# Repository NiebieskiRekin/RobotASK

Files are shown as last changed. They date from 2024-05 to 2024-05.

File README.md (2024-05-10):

# Robot ASK - Piano tiles

A Piano Tiles (mobile game) hardware autoclicker built on the ATmega328. All electrical sketches and the PCB were designed in [KiCad](https://www.kicad.org/). Code for the microprocessor was written in C++ using Arduino and Servo libraries as well as the [PlatformIO](https://platformio.org/install/ide?install=vscode) VSCode extension.

This project also has a live visualisation Python script that communicates with the main board over serial to display data captured by the photoresistor module. This script can also be used to quickly adjust some parameters at the start of runtime.

This repository was created for a university group project for [RoboDay 2024](https://www.facebook.com/events/1518830758974874) at Poznań University of Technology.
Made by: Tomasz Pawłowski, Jakub Kamieniarz, Jakub Buler, Adam Deter  

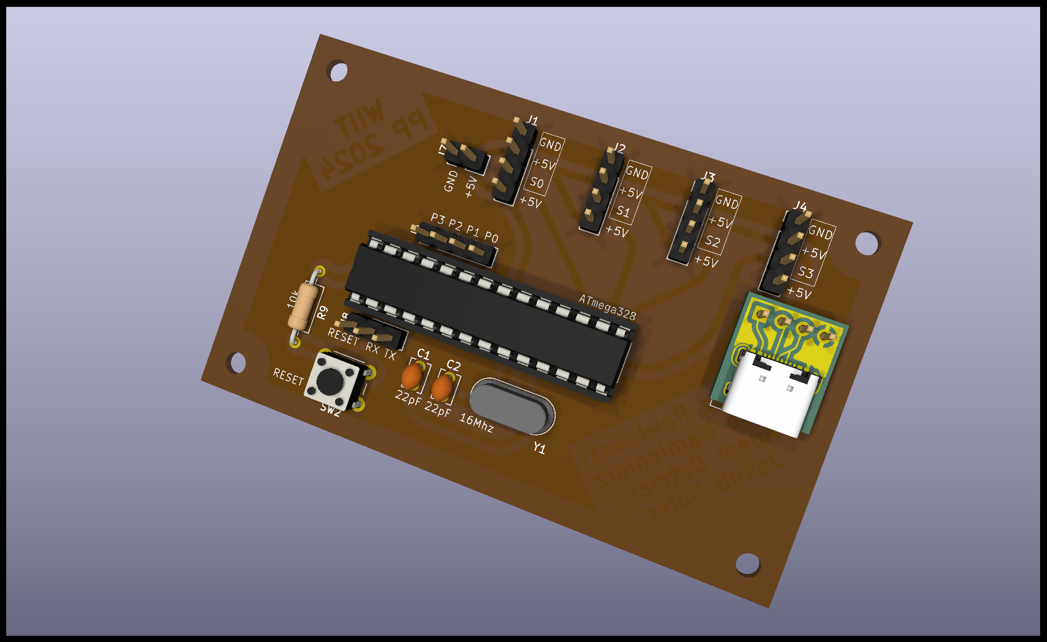
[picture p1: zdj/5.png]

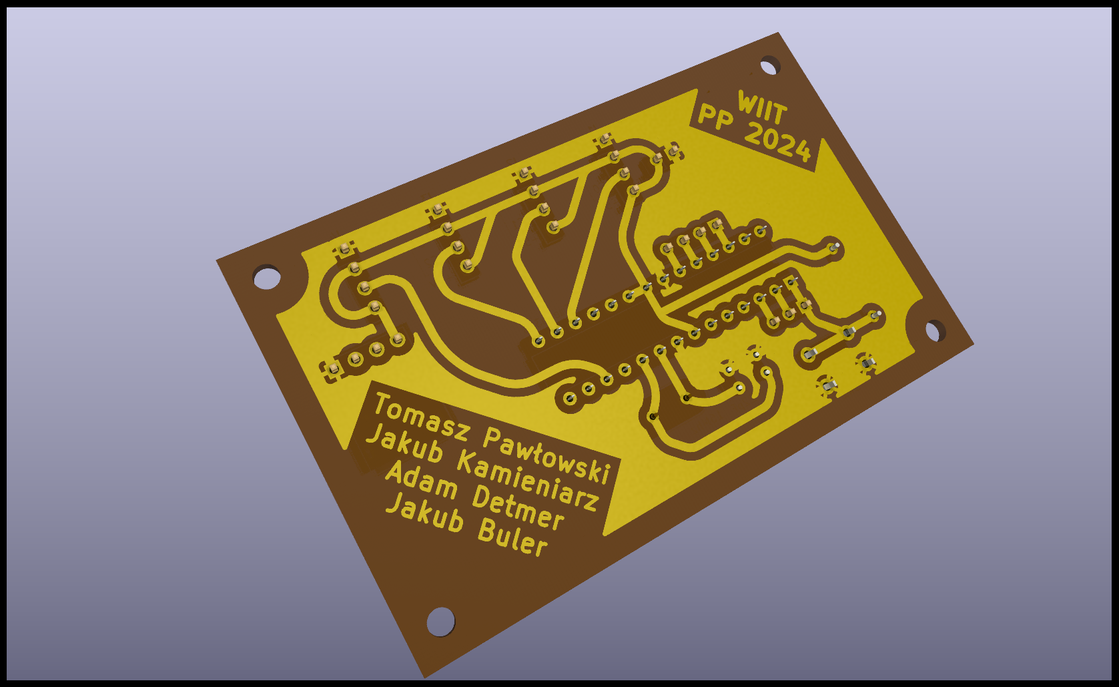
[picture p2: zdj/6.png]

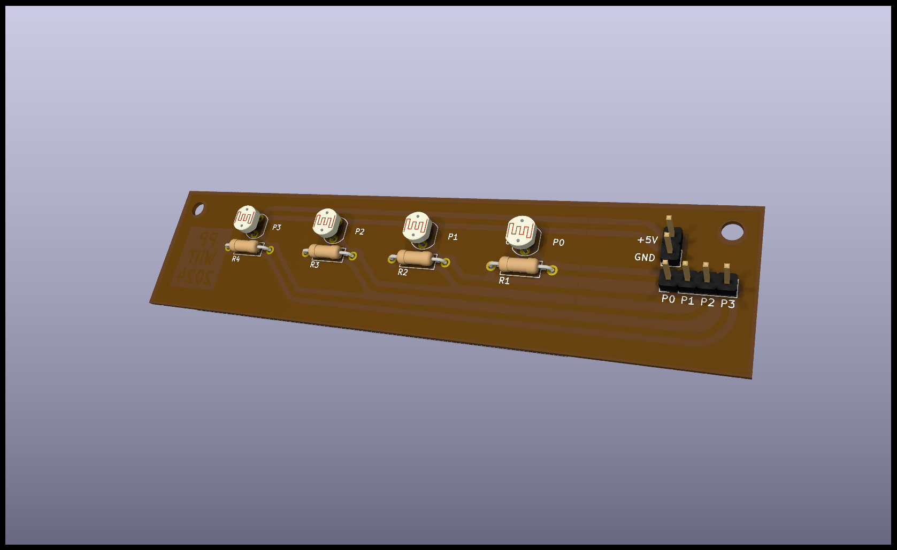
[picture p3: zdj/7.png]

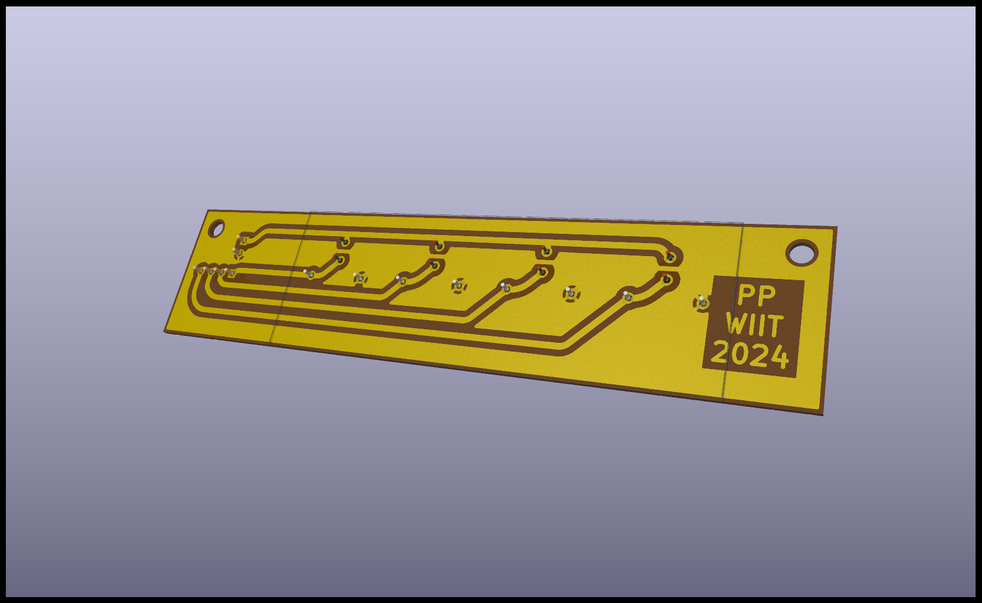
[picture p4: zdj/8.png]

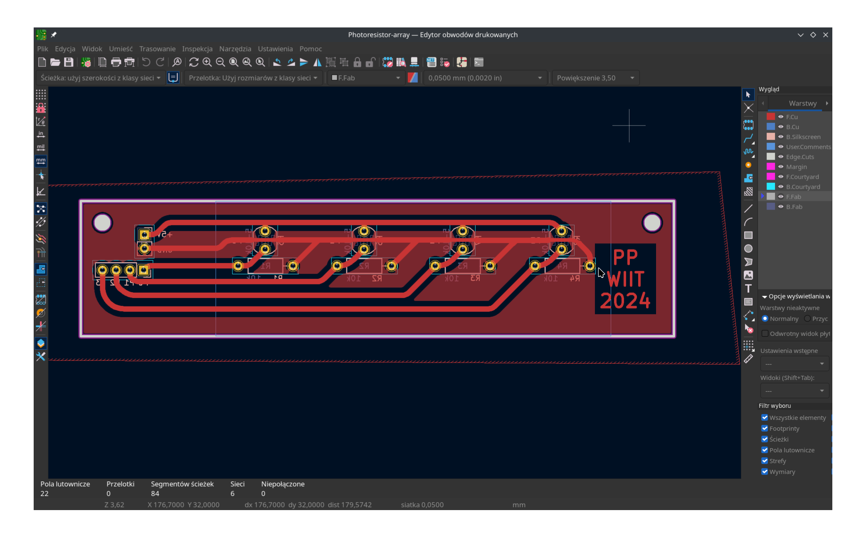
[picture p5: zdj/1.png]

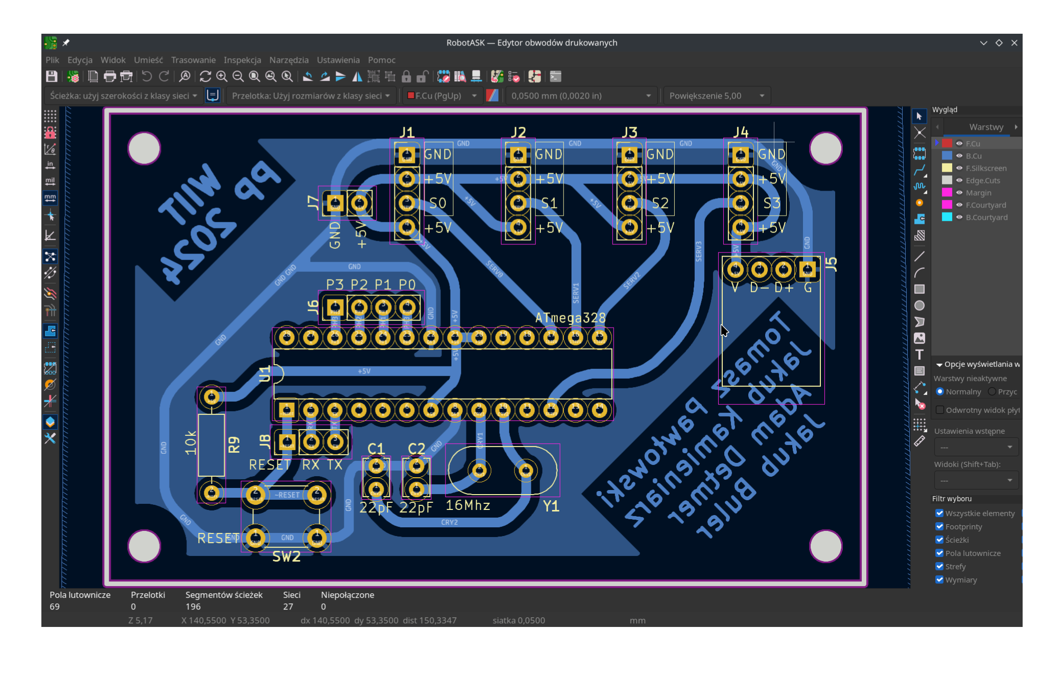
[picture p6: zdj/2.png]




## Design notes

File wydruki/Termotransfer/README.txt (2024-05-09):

Wydruk na papierze kredowym na drukarce laserowej.
Płytka z fotorezystorami jest ma piny po przeciwnej stronie względem rezystorów

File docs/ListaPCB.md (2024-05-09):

# Lista do wytrawiania PCB

## Wymiary laminatu z miedzią:
- co najmniej o 5mm dłuższe i szersze od każdej krawędzi płytki

układ 

#### Wymiary głównej płytki:
- wszerz (x) 80mm
- wzdłuż (y) 50mm
- wzwyż (z) min. 6mm (potencjalnie więcej ze względu na wpinane przewody do pinów)
- otwory na komponenty 1mm

#### Otwory na przykręcenie głównej płytki:
- średnica 3mm
- odległość środka od krawędzi 3mm
- odległość wszerz (x) pomiędzy otworami (środki) 74mm
- odległość wzdłuż (y) pomiędzy otworami (środki) 44mm

#### Wymiary płytki z fotorezystorami:
- długość płytki (x) 110 mm
- szerokość płytki (y) 17mm
- odległość pomiędzy fotorezystorami (środki) 18,325mm
- szerokość ekranu 73,3mm
- otwory na goldpiny o średnicy 1mm
- otwory na rezystory i fotorezystory 0,8mm

#### Otwory na przykręcenie płytki z fotorezystorami:
- średnica 3mm
- odległość środka od krawędzi 3mm
- odległość wszerz (x) pomiędzy środkami otworów 104mm
- odległość lewego otworu (obok pinów) do krawędzi ekranu 22mm
- odległość prawego otworu (obok napisu) do krawędzi ekranu 8,7mm
- odległość krawędzi pinu (czarnej podstawy) do krawędzi ekranu 12mm

## Wariant 1: Termotransfer
[filmik (pl)](https://www.youtube.com/watch?v=1L4GrPDR9TE)

### Lista rzeczy:

- [ ] rękawiczki i okulary ochronne
- [ ] wytrawiacz, jeden z:
  - nadsiarczan sodu
  - chlorek żelaza
  - kwas azotowy
- [ ] proszek do prania xd
- [ ] zamiennie
  - rozpuszczalnik nitro
  - benzyna ekstrakcyjna
- [ ] lejek
- [ ] plastikowa butelka (1.5l)
- [ ] plastikowa kuweta (pojemnik bez wieczka)
- [ ] laminat z jedną wartstwą miedzi (miedziana blaszka jakby)
- [ ] wodny papier ścierny
- [ ] gąbka kuchenna + mleczko do mycia (cif)
- [ ] żelazko z płaską powierzchnią grzejącą (bez pary)
- [ ] linijka + ekierka duża
- [ ] pilnik (taki do metalu)
- [ ] zamiennie
  - nożyce do laminatu
  - piłka do metalu
  - nożyk do tapet i dużo cierpliwości
- [ ] zwykłe nożyczki do papieru
- [ ] świeża szczoteczka
- [ ] ołówek
- [ ] wydruk płytki na papierze kredowym z drukarki laserowej w lustrzanym odbiciu (bez negatywu)

## Wariant 2: UV
[filmik 1 (ang)](https://www.youtube.com/watch?v=1C3k6dyVN18)
[filmik 2 (ang)](https://www.youtube.com/watch?v=xyBgbNPrWg8)

### Lista rzeczy 

to

- [ ] chemia ze zdjęcia
- [ ] laminat z warstwą miedzi
- [ ] alkohol do mycia i ściereczka
- [ ] papier ścierny
- [ ] wydruk pcb na zwykłej kartce papieru z drukarki atramentowej w odbiciu i w negatywie (high quality)
- [ ] nożyk do tapet
- [ ] dry film roll (sucha folia światłoczuła? [to](https://allegro.pl/oferta/portable-photosensitive-dry-film-pcb-in-roll-for-circuit-board-1m-blue-12340601866))

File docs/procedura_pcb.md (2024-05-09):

# Procedura pcb
1. oczyść płytkę za pomocą gąbki lub papieru ściernego
2. wydruk w negatywie i odbiciu na papierze (jaka drukarka?)
3. przytnij płytkę do wymiaru
4. naklej folię światłoczułą na plytkę
5. pozbądź się bąbelków suszarką / żelazkiem
6. na płytkę z folią posmarowaną na wierzchu olejkiem nałóż wydruk płytki tuszem do dołu
7. UV (nwm ile czasu)
8. przepłucz płytkę w roztworze NaOH lub NaCO3 ???
9. przepłucz płytkę pod bieżącą wodą
10. zakryj dziury markerem pernamentnym
11. wytrawianie płytki w FeCl3
12. oczyszczenie płytki w acetonie+szczoteczka lub NaOH znowu

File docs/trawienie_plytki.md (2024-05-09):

# Podsumowanie trawienia płytki

## Etapy:
1. Oczyszczenie warstwy miedzi z płytki wodnym papierem ściernym oraz potem alkoholem
2. Przycięcie płytki do wymiaru z zapasem za pomocą tępej strony nożyka do tapet
3. Naklejenie folii światłoczułej na płytkę bez bąbli powietrza (suszarka oddalona o parę cm), odklejenie warstwy ochronnej za pomocą taśmy malarskiej
4. Nałożenie kartki papieru z wydrukiem z drukarki laserowej na folię pokrytą olejem
5. 159 sekund naświetlania lampą UV 36W, potem odklejenie drugiej folii ochronnej
6. [nieudane] Wywołanie płytki w roztworze 1% masowych NaOH z wodą (200ml, szczoteczka, bujanie na boki), przepłukanie wodą
	- Roztwory o wyższym stężeniu (np. 5%, 2/3 łyżki stołowej na pół litra wody) sprawnie usuwają całą folię, nadają się do ostatniego etapu
	- Roztwory o niższym stężeniu (poniżej 1%) działają zbyt długo, przez co folia ulega zniszczeniu
	- Trzymanie w roztworze powyżej 2min ogólnie niszczy folię i zaciera ścieżki 
	- Przetarcie delikatne włosiem szczoteczki pomaga przyśpieszyć proces i zdjąć odpowiednie warstwy na początku, ale w momencie gdy jest już widoczna miedź to tylko psuje dalej folię
	- roztwór sody oczyszczonej (NaHCO3, słaba zasada) w żadnym stężeniu nie przyniósł efektu 
7. Wytrawianie płytki w roztworze 25% masowych FeCl3 z wodą (200ml roztworu, bujanie na boki) aż do momentu zupełnego pozbycia się śladów miedzi z pól gdzie jej nie powinno być. Przepłukanie wodą
8. Zmycie pozostałej folii w acetonie technicznym lub 5% NaOH + szczoteczka. Przepłukanie wodą
9. [nieosiągnięte] Wytrawiona płyka gotowa, nawiercenie otworów, docięcie i przeszlifowanie krawędzi płytki, wlutowanie komponentów

## Pomysły na etap nr 6
- [ ] przetestowanie innego wywoływacza (Na2CO3 lub Na2SiO3)
- [ ] pozostawienie płytki po ekspozycji UV na 10-30 min w ciemnym miejscu przed wywołaniem
- [ ] skrócenie lub przedłużenie ekspozycji UV
- [ ] przeniesienie procesów do ciemniejszego pomieszczenia
- [ ] przerobienie schematu płytki na wieksze ścieżki i odstępy między nimi
- [ ] wydruk na kalce technicznej 90g/m^2, wyższej jakości, zaczernienie nad oparami acetonu
- [ ] użycie innego oleju (np. mineralnego) zamiast rzepakowego

## Inne notatki
- aby zmyć folię acetonem to trzeba zanurzyć płytkę na kilkadziesiąt sekund i zetrzeć mechanicznie
- olej rzepakowy (kujawski itd) sprawdza się dobrze do nakładania wydruku na folię, aby zapewnić przezroczystość
- dopóki płytka nie przeszła wytrawiacza to nieudany etap wywoływania można przywrócić do kroku 3. naklejania folii światłoczułej poprzez zmycie resztek folii acetonem
- poszukaj więcej plastikowych łyżek i łyżeczek oraz uszykuj baniaki z wodą 
- prażenie sody oczyszczonej (NaHCO3) daje węglan sodu (Na2CO3), który ma silny odczyn zasadowy i może przyniesie lepszy efekt
- w tutorialach używane są lampy o dużo słabszej mocy i różnym czasie naświetlania (jedni piszą 20 sekund inni 10 minut)
	- stary skaner z zamontowanymi w środku czterema świetlówkami UV 9W przez 25s
	- lampa do tipsów 9W przez 15-20s

	> "Po naświetleniu zrywam folię przezroczystą z nalepionej na płytkę folii światłoczułej i odkładam płytkę w ciemne miejsce na 10 minut. Jest to konieczne, aby zaszły pewne procesy w polimerze"

	> "Ustawiamy czas naświetlania. Jeżeli nasza naświetlarka nie ma możliwość ustawiamy minutnik na 2 do 4 minut. Czas jaki jest potrzebny zależy od naszej naświetlarki a dokładniej żarówek jakie zastosowaliśmy. Po naświetlaniu zostawić płytkę w ciemni na około 30 min. Może to być również szczelne pudełko lub inne ciemne miejsce gdzie promienie światła ani słońca nie będą mogły dojść do płytki."

- Wydruk wyższej jakości na kalce technicznej 90g/m^2 - grubszy papier

> "Następny krok to nawiercanie. Wszystkie dziurki robię na wiertarce ze statywem wiertłami z węglika VHM. Prędkość wrzeciona to 20 tys. obrotów na minutę oraz posuw w osi Z 150mm/min" 

- Praca nad płytką od momentu oczyszczenia płytki wykonywana w piwnicy lub łazience aż do momentu wytrawienia w wytrawiaczu
- powszechnie używane wywoływacze:
	- metakrzemian disodu (Na2SiO3, ten z woreczka "wywoływacz"), [przykladowy link](https://www.tme.eu/pl/details/uni-dev-22g/materialy-do-produkcji-plytek-drukow/ag-termopasty/art-agt-087/), roztwór 10g/1l
	- soda kalcynowana (Na2CO3), **prażona** soda oczyszczona, niżej proces prażenia, Stężenie roztworu wywoływacza to 5g na 0,5 l wody, 
	- do folii nie nadaje się żaden roztwór NaOH 

> "soda kalcynowana, którą można kupić w sklepach internetowych lub wykonać samodzielnie z sody oczyszczonej: blachę wyłożyć papierem do pieczenia, wysypać sodę i wstawić do rozgrzanego do 200 stopni C piekarnika na godzinę" [link](https://zielonyogrodek.pl/dom-i-balkon/porady-domowe/15606-czy-mozesz-samodzielnie-zrobic-tabletki-do-zmywarki-tak-i-to-bardzo-latwo-oto-nasze-przepisy)

- użycie lepszego środka do sprawienia że kartka zrobi się przezroczysta na folii
	- naj. oleje mineralne
	- baby oil
	- WD40/transparent

> "Jak folia jest negatywowa, to wywoływaczem jest węglan sodu, jak pozytywowa to wodorotlenek sodu lub metakrzemian. "

## Tutoriale:
1. [https://www.leniwiec.org/2014/03/02/moja-metoda-robienia-pcb-metoda-fotochemiczna-z-soldermaska-cynowaniem-i-opisami/ ](https://www.leniwiec.org/2014/03/02/moja-metoda-robienia-pcb-metoda-fotochemiczna-z-soldermaska-cynowaniem-i-opisami/ )
2. [http://gotronik.com/2019/09/18/jak-zrobic-plytke-pcb-metoda-fotochemiczna/](http://gotronik.com/2019/09/18/jak-zrobic-plytke-pcb-metoda-fotochemiczna/)
3. [https://www.elektroda.pl/rtvforum/topic2527723.html](https://www.elektroda.pl/rtvforum/topic2527723.html)
4. [https://www.elektroda.pl/rtvforum/topic2714312.html](https://www.elektroda.pl/rtvforum/topic2714312.html)

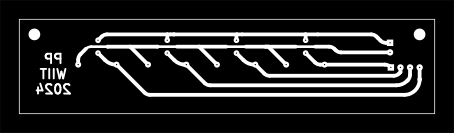
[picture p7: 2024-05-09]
wydruki/UV/new/g3.png

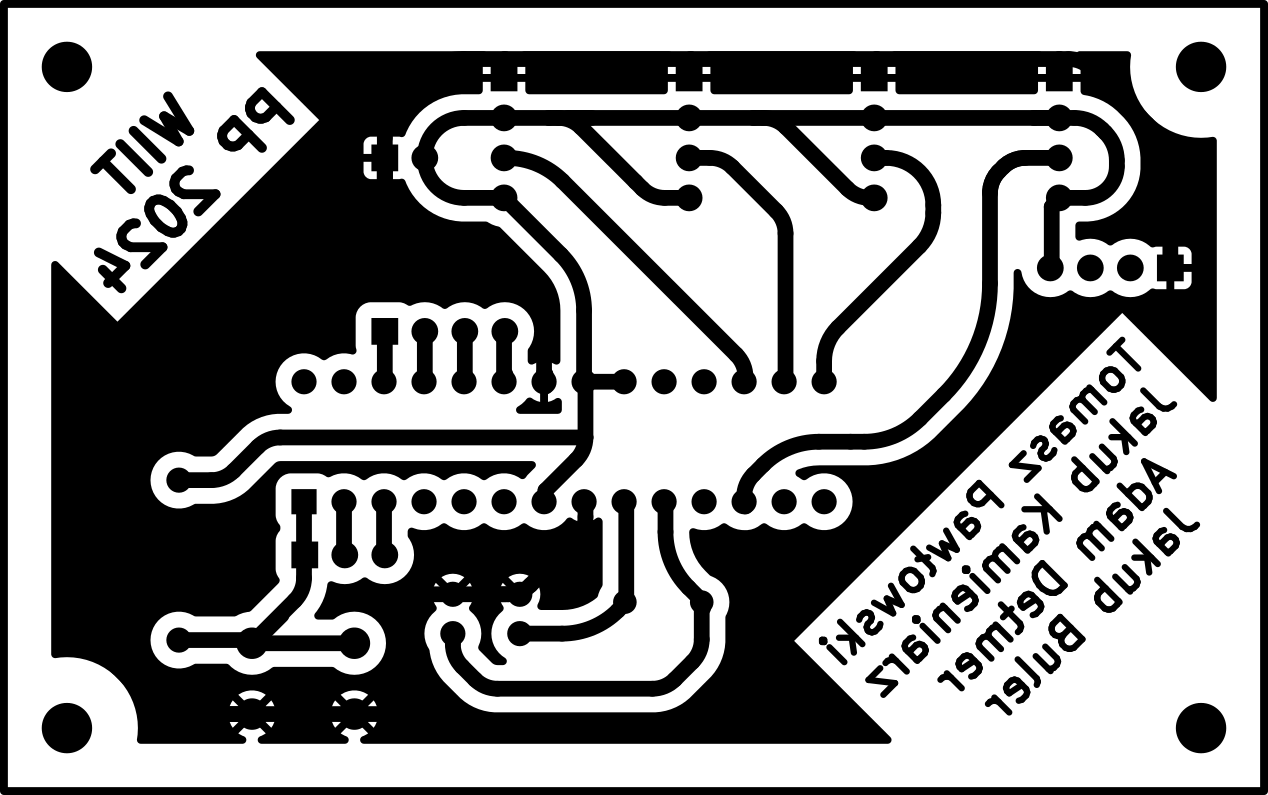
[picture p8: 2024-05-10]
wydruki/Termotransfer/v2/RobotASK-B_Cu.png

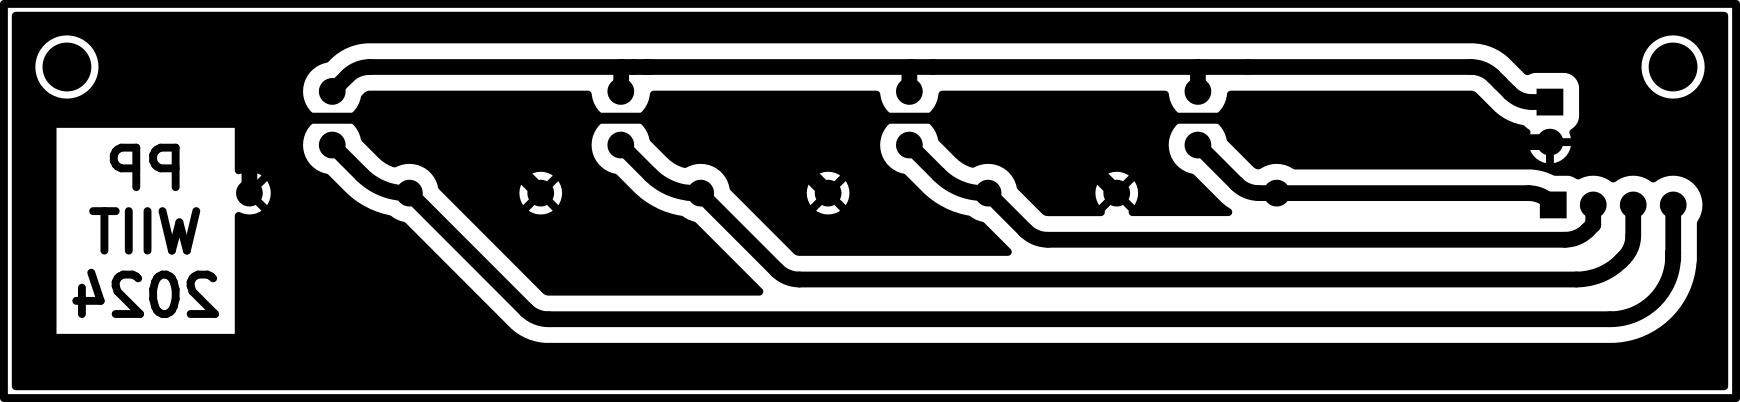
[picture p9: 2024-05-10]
wydruki/Termotransfer/v2/Photoresistor-array-F_Cu.png

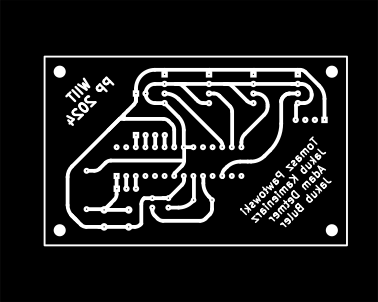
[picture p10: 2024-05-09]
wydruki/UV/new/g2.png

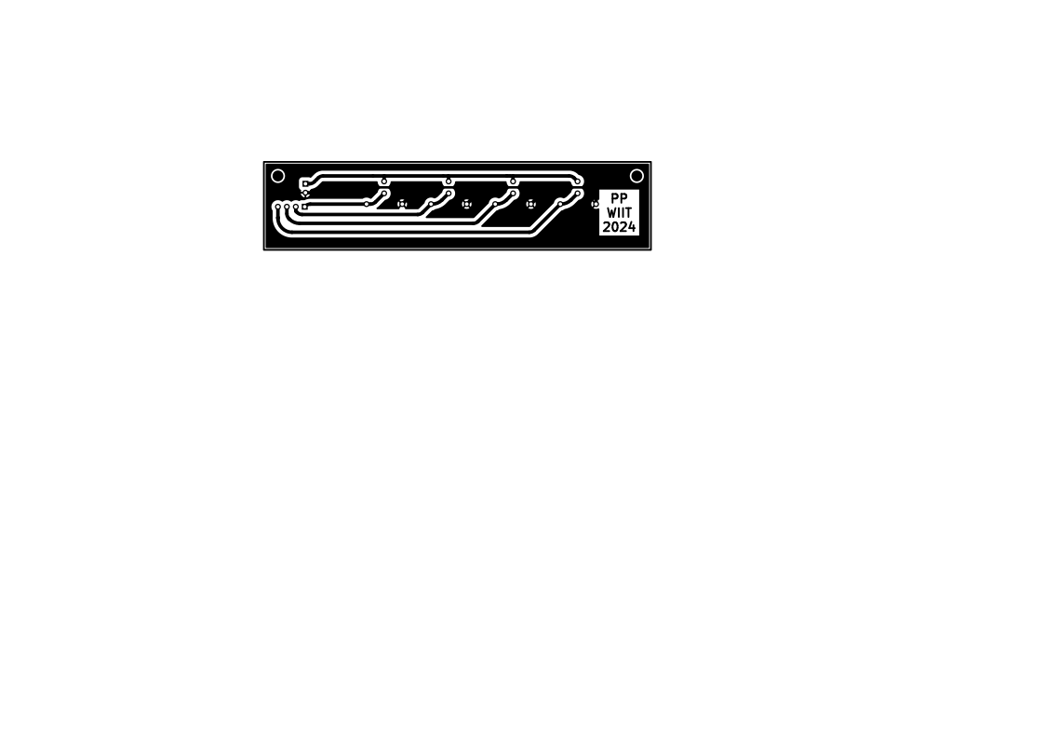
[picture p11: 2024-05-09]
wydruki/wiercenia/Photoresistor-array-skala-1-znaczniki.png

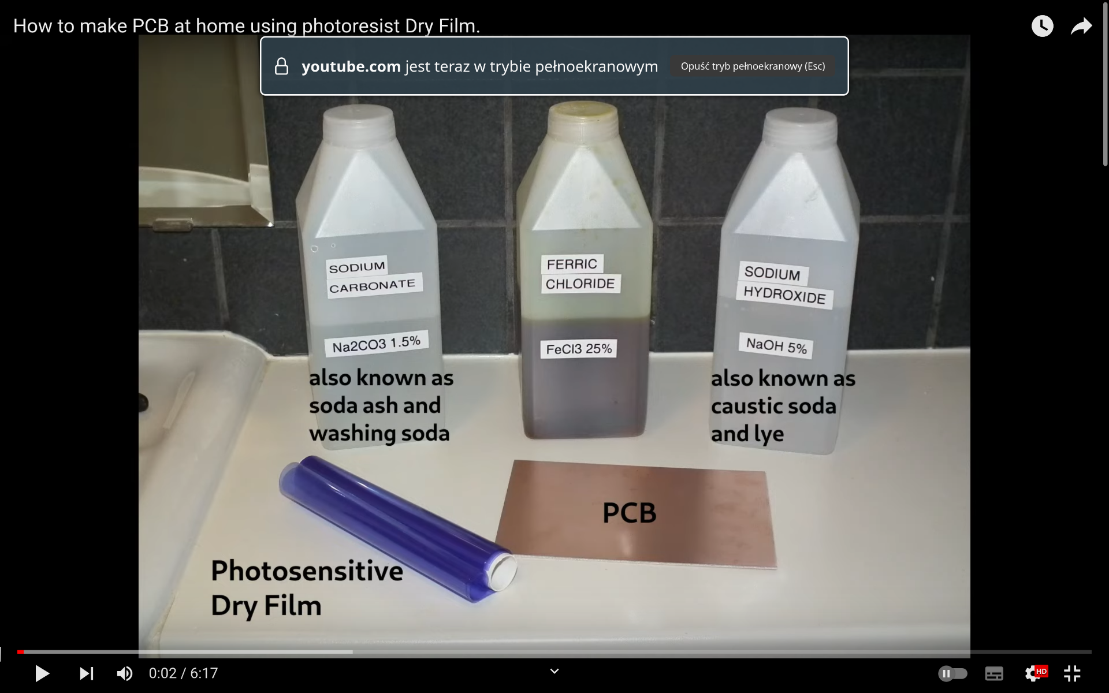
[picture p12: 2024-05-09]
zdj/lista_uv_2.png

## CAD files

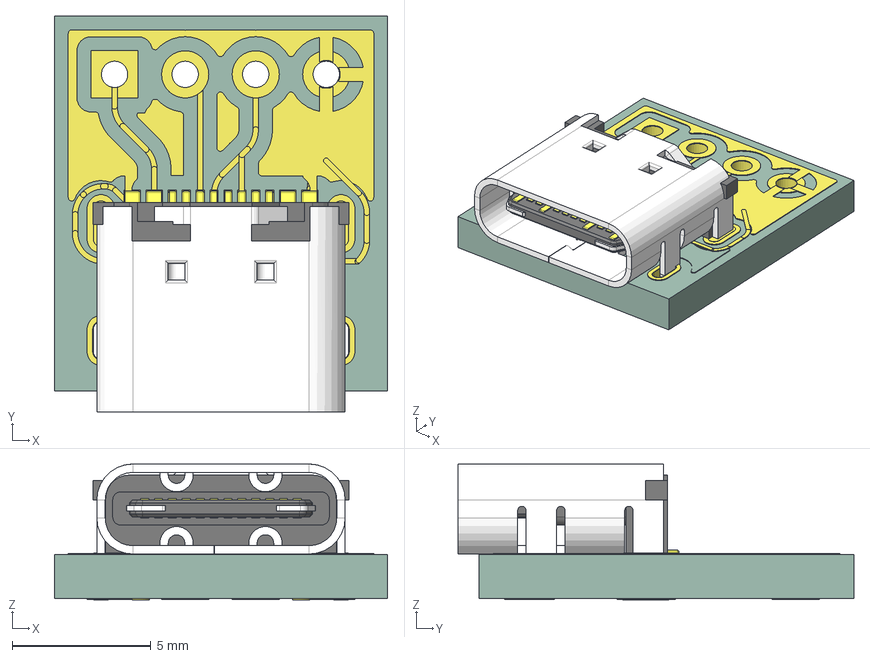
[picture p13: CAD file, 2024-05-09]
KiCad/RobotASK/usb-c-socket/usb-c-socket.step
12.0 x 14.3 x 4.90 mm
USB_type_C_12p
usb-c-socket_track_1
usb-c-socket_track_2
usb-c-socket_track_3
usb-c-socket_track_4
usb-c-socket_track_5
usb-c-socket_track_6
usb-c-socket_track_7
usb-c-socket_track_8
usb-c-socket_track_9
usb-c-socket_track_10
usb-c-socket_track_11
usb-c-socket_track_12
usb-c-socket_track_13
usb-c-socket_track_14
usb-c-socket_track_15
usb-c-socket_track_16
usb-c-socket_track_17
usb-c-socket_track_18
usb-c-socket_track_19
usb-c-socket_track_20
usb-c-socket_track_21
usb-c-socket_track_22
usb-c-socket_track_23
usb-c-socket_track_24
usb-c-socket_track_25
usb-c-socket_track_26
usb-c-socket_track_27
usb-c-socket_track_28
usb-c-socket_track_29
usb-c-socket_track_30
usb-c-socket_track_31
usb-c-socket_track_32
usb-c-socket_track_33
usb-c-socket_track_34
usb-c-socket_track_35
usb-c-socket_track_36
usb-c-socket_track_37
usb-c-socket_track_38
usb-c-socket_zone_1
usb-c-socket_zone_2
usb-c-socket_zone_3
usb-c-socket_zone_4
usb-c-socket_pad_1
usb-c-socket_pad_2
usb-c-socket_pad_3
usb-c-socket_pad_4
usb-c-socket_pad_5
usb-c-socket_pad_6
usb-c-socket_pad_7
usb-c-socket_pad_8
usb-c-socket_pad_9
usb-c-socket_pad_10
usb-c-socket_pad_11
usb-c-socket_pad_12
usb-c-socket_pad_13
usb-c-socket_pad_14
usb-c-socket_pad_15
usb-c-socket_pad_16
usb-c-socket_pad_17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

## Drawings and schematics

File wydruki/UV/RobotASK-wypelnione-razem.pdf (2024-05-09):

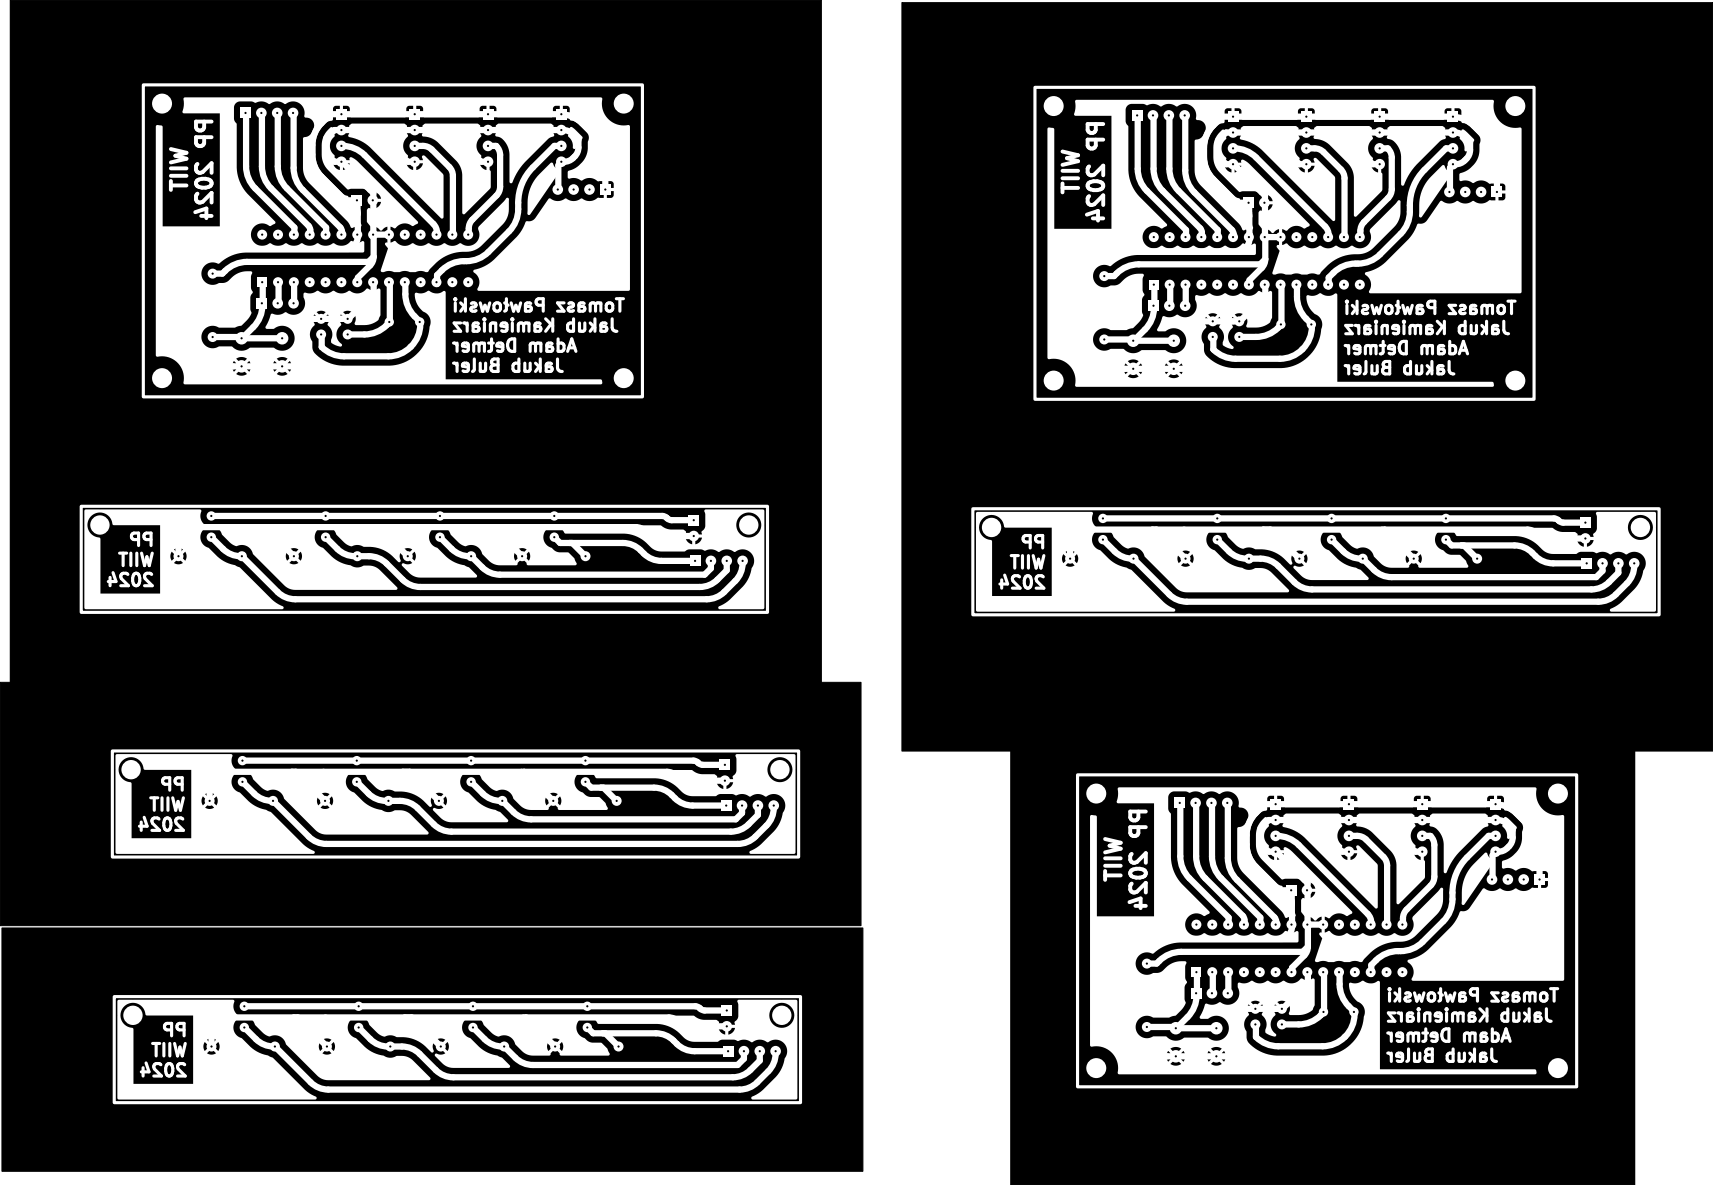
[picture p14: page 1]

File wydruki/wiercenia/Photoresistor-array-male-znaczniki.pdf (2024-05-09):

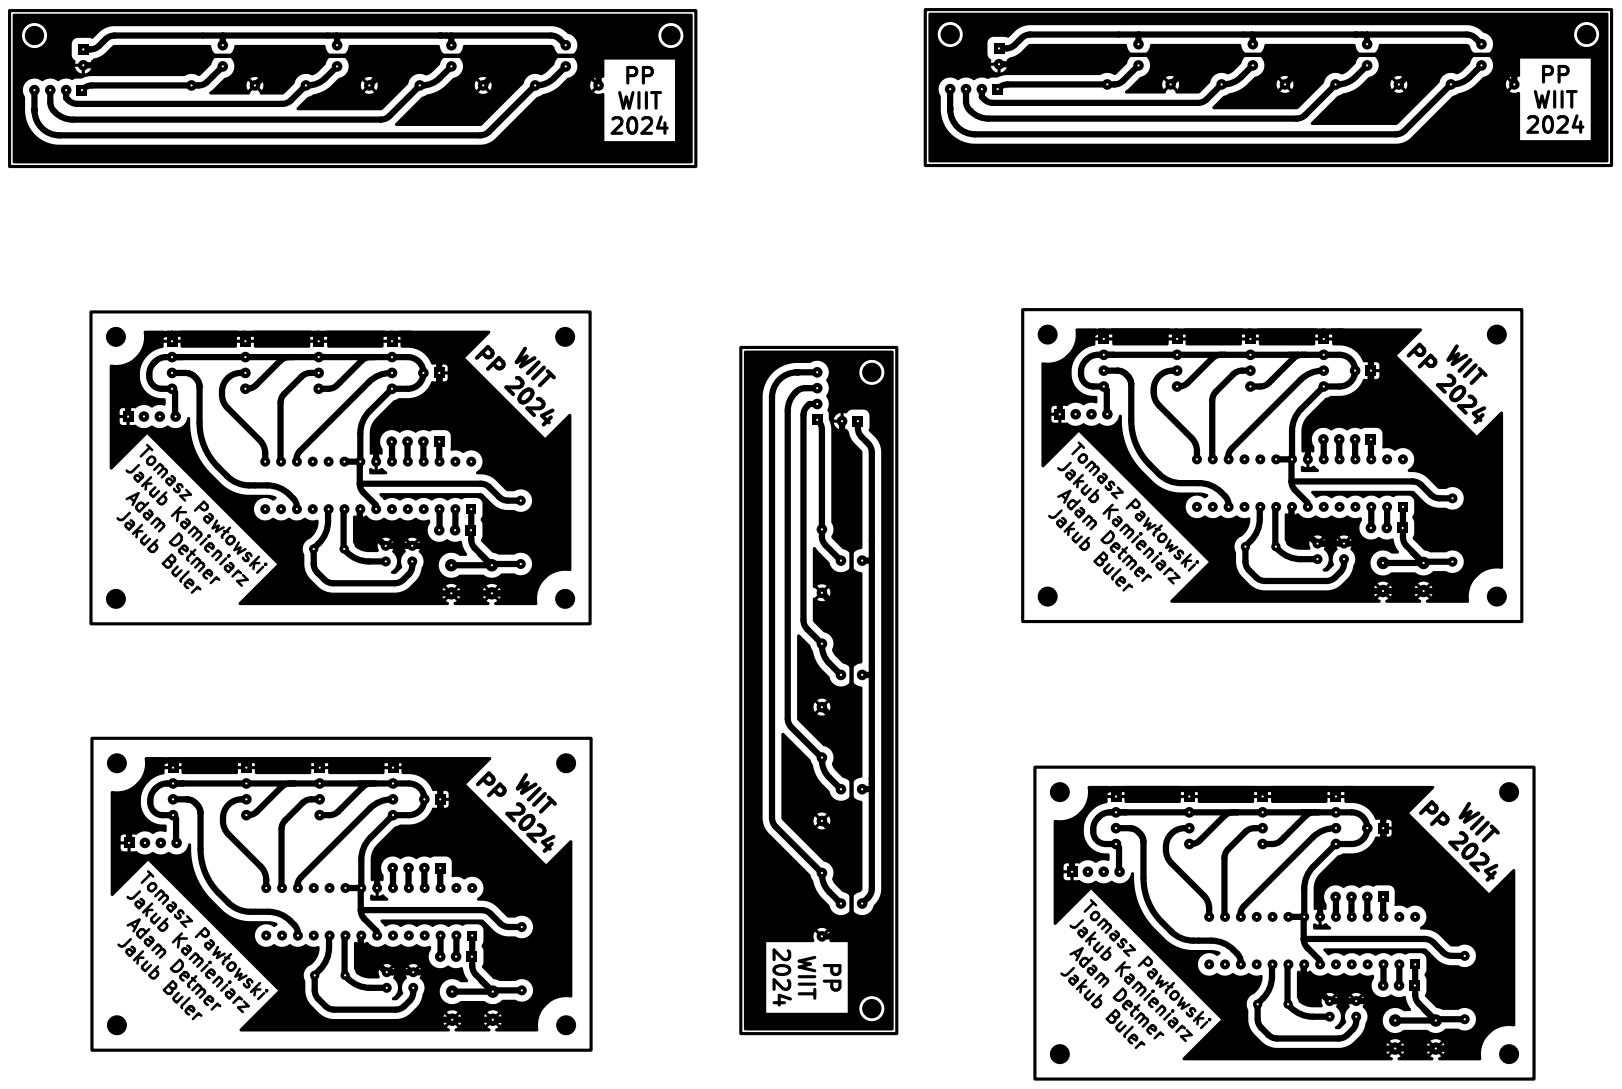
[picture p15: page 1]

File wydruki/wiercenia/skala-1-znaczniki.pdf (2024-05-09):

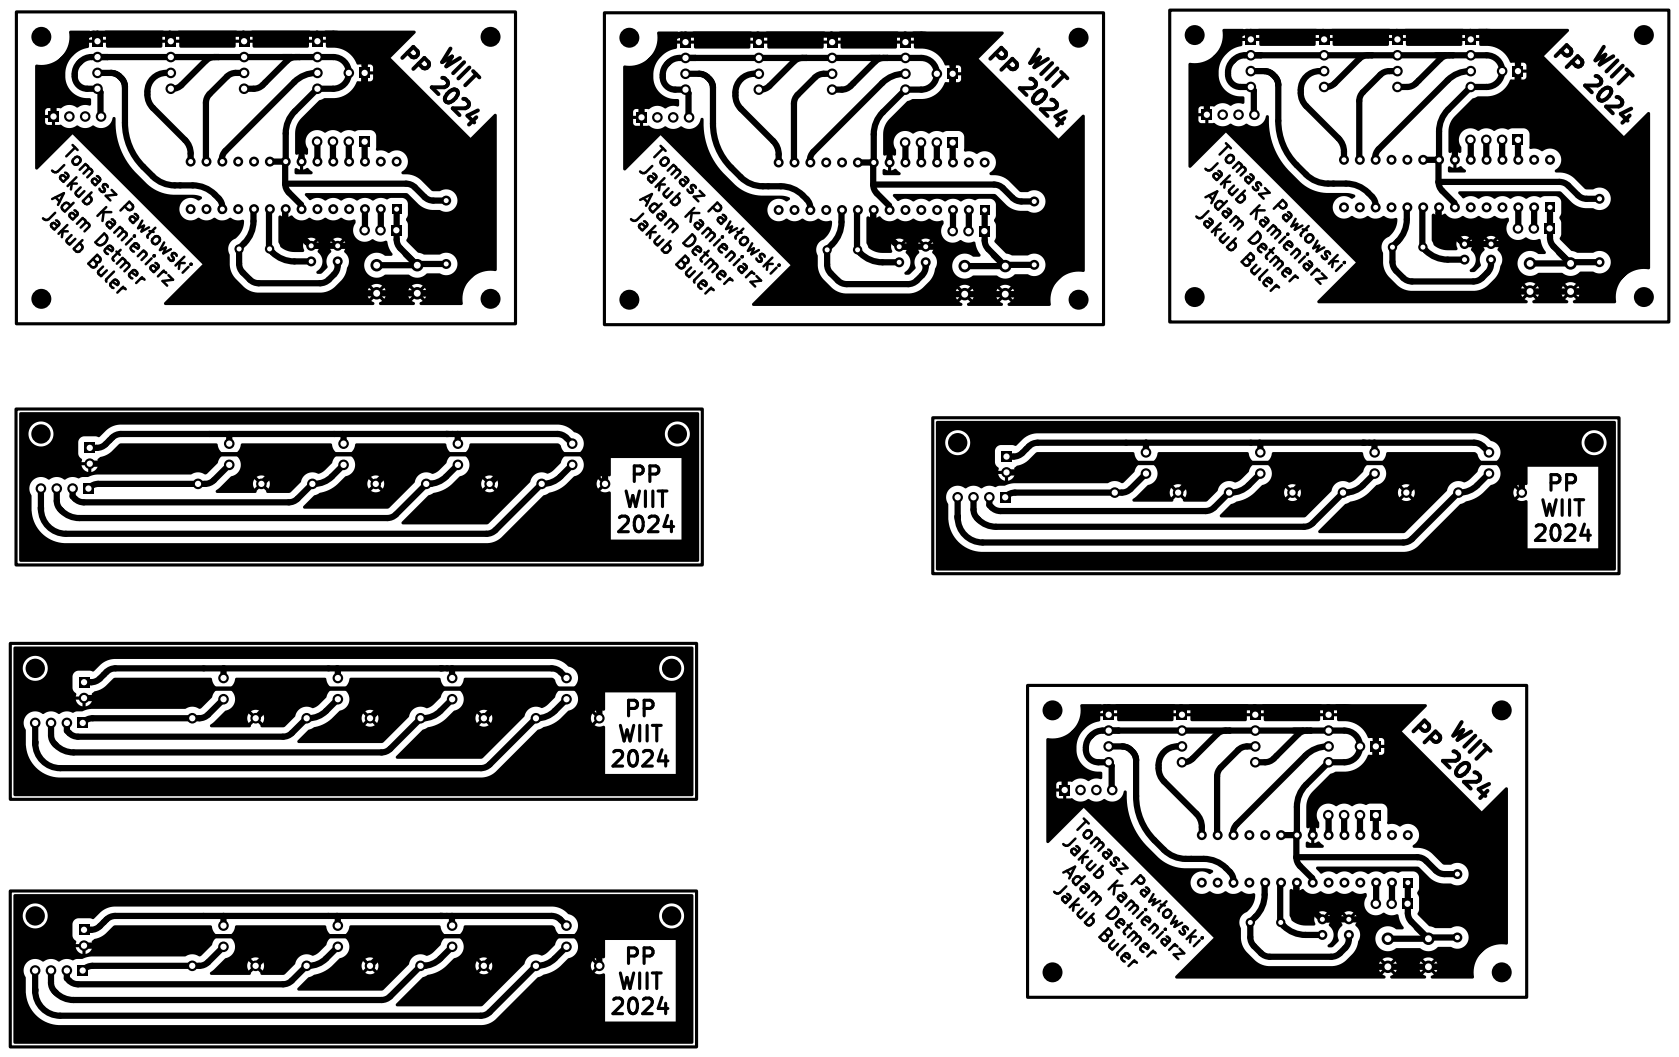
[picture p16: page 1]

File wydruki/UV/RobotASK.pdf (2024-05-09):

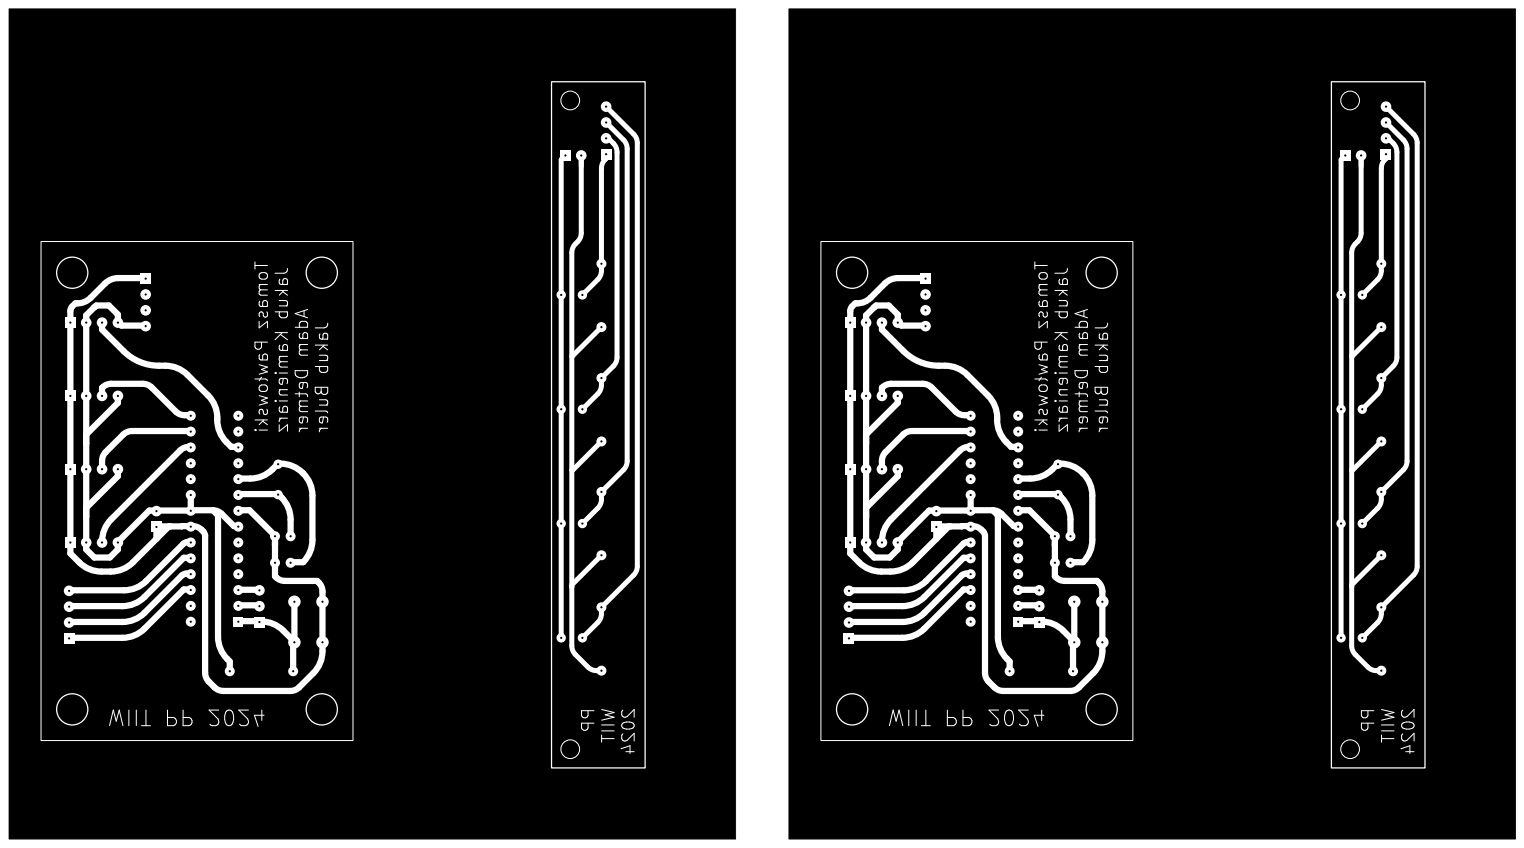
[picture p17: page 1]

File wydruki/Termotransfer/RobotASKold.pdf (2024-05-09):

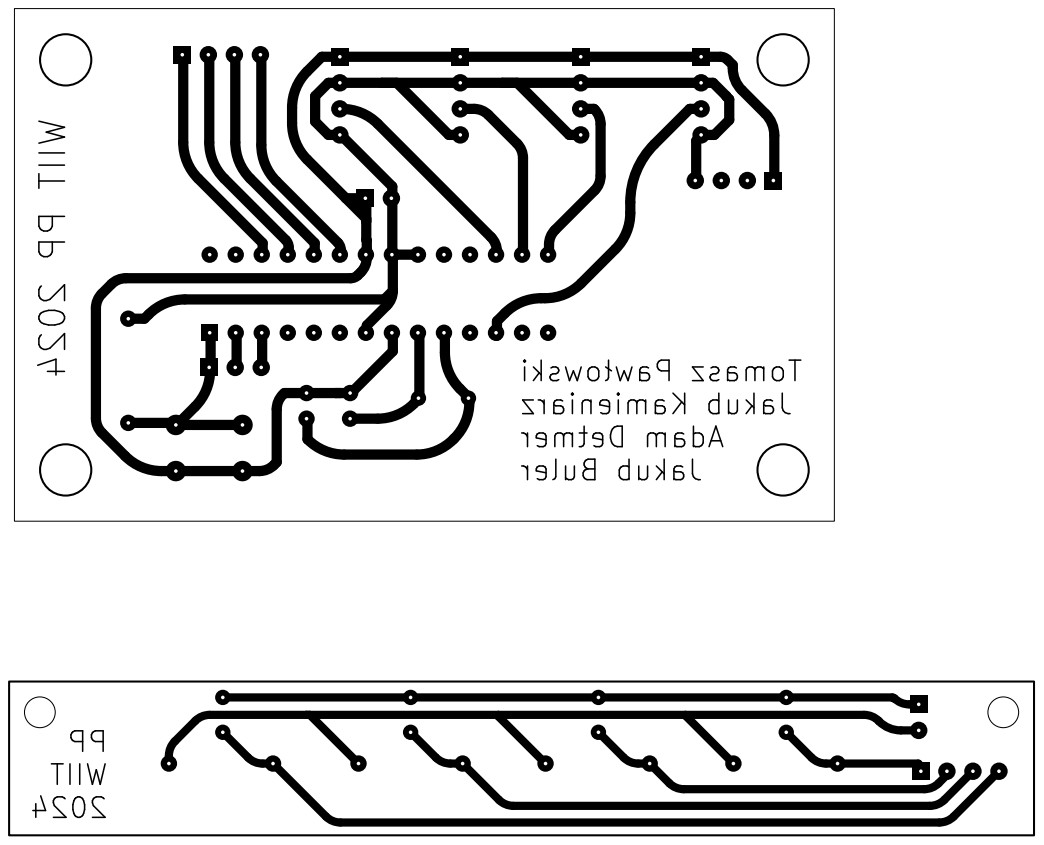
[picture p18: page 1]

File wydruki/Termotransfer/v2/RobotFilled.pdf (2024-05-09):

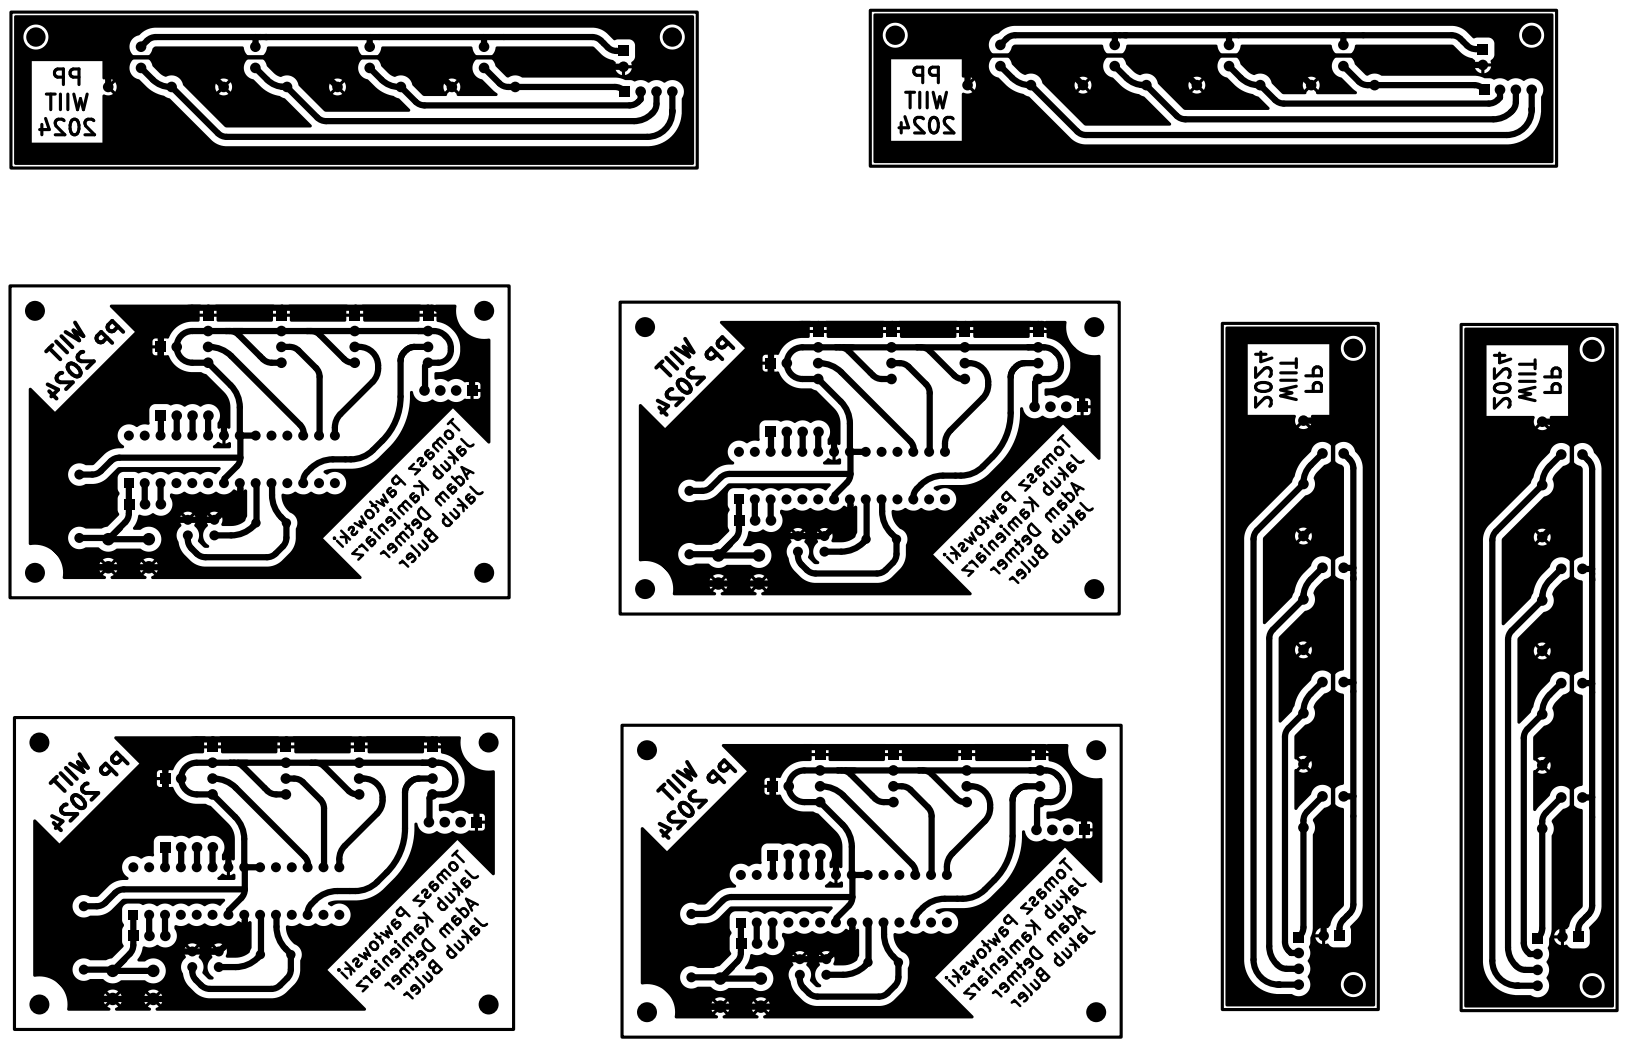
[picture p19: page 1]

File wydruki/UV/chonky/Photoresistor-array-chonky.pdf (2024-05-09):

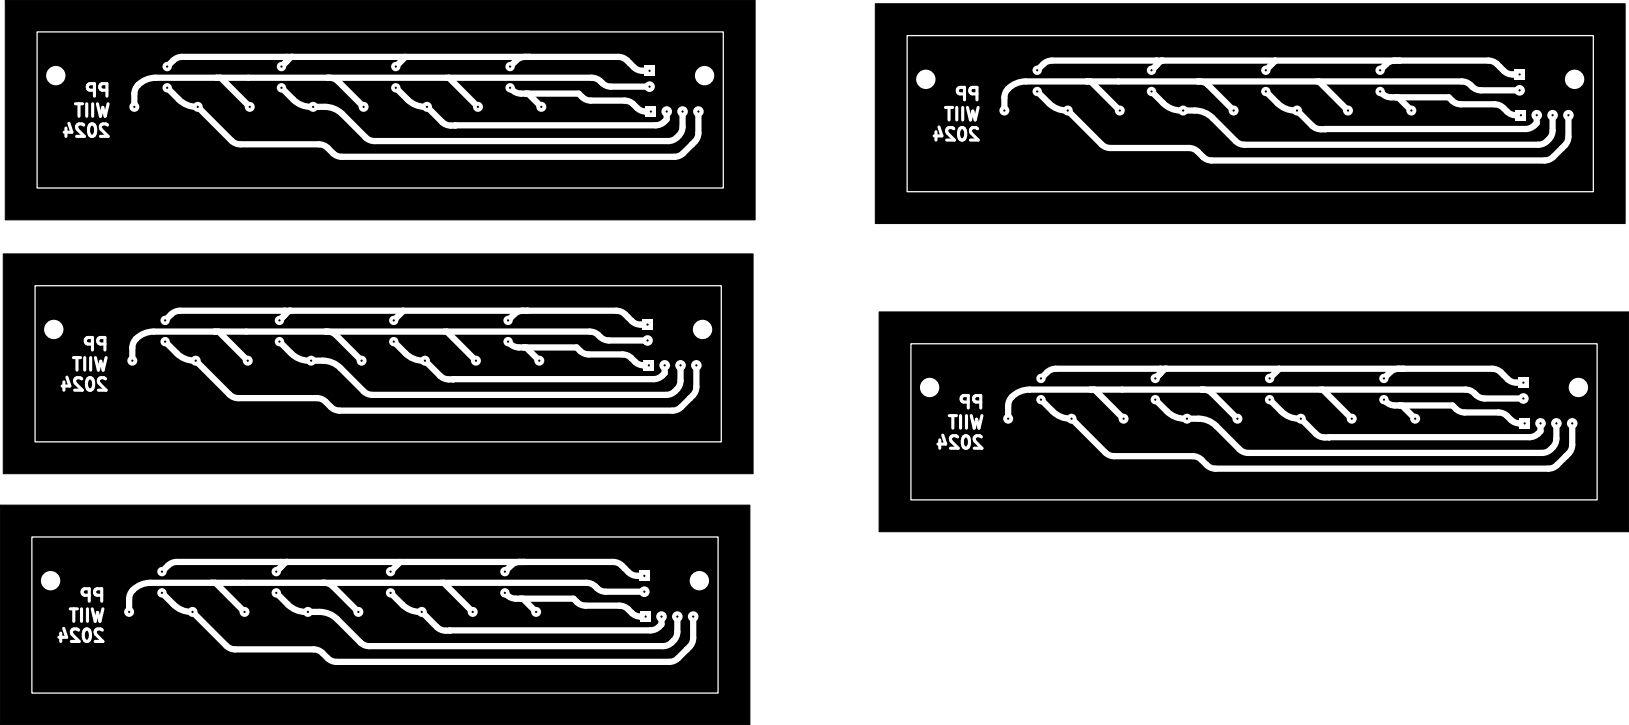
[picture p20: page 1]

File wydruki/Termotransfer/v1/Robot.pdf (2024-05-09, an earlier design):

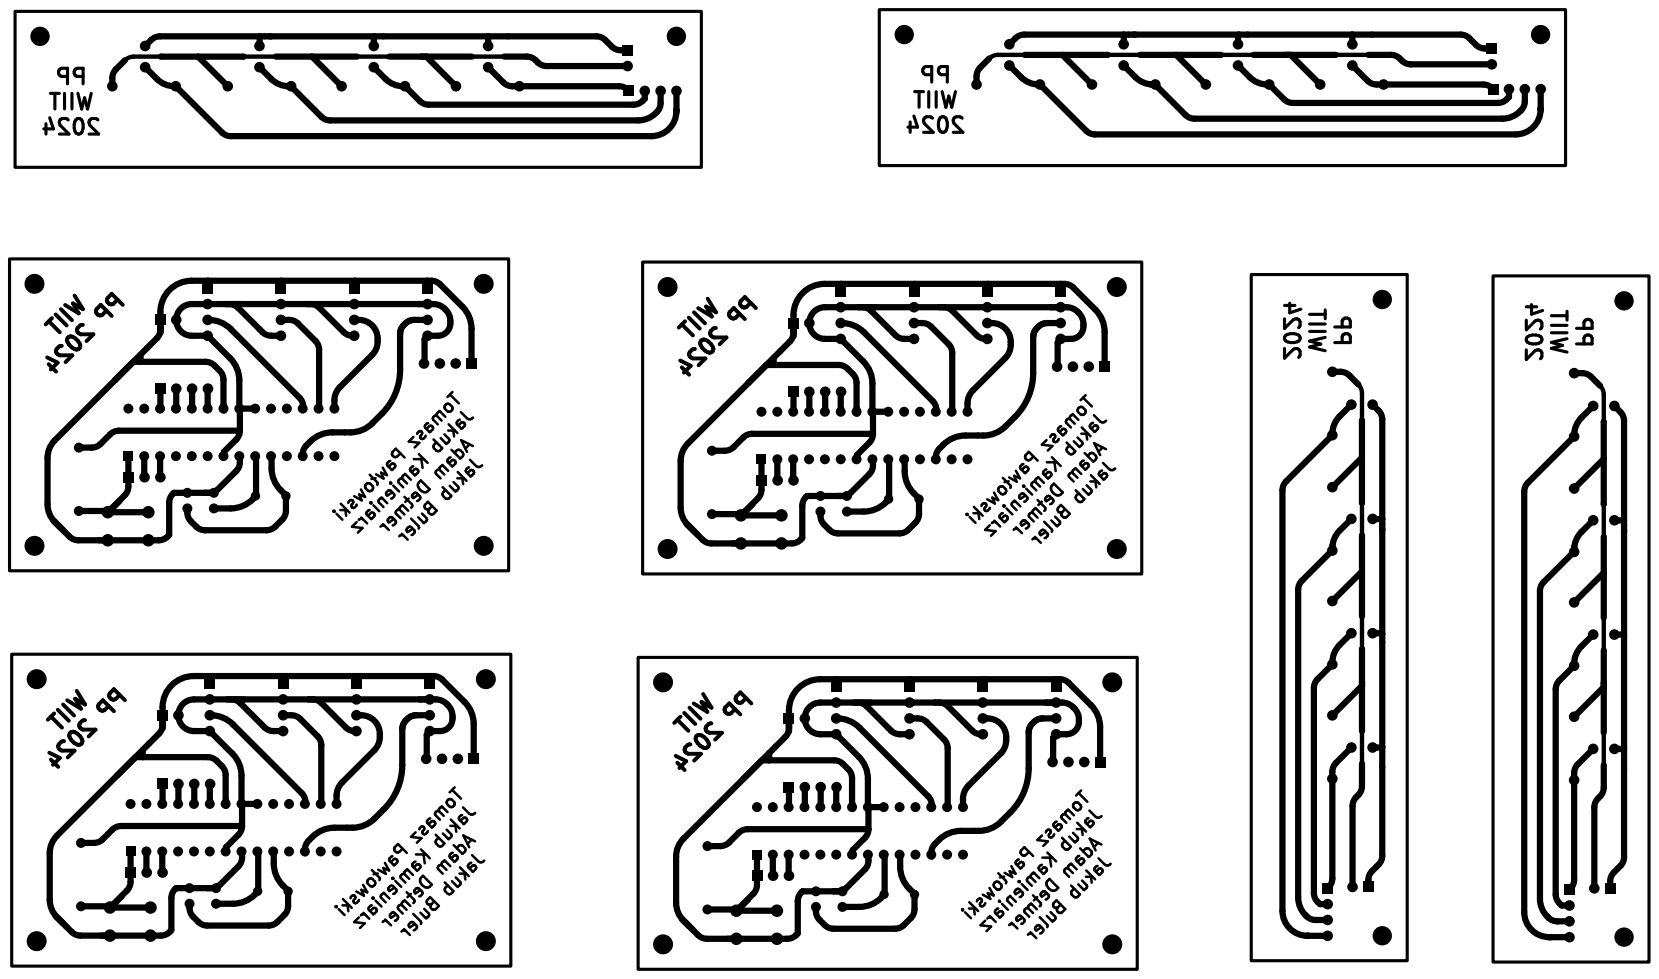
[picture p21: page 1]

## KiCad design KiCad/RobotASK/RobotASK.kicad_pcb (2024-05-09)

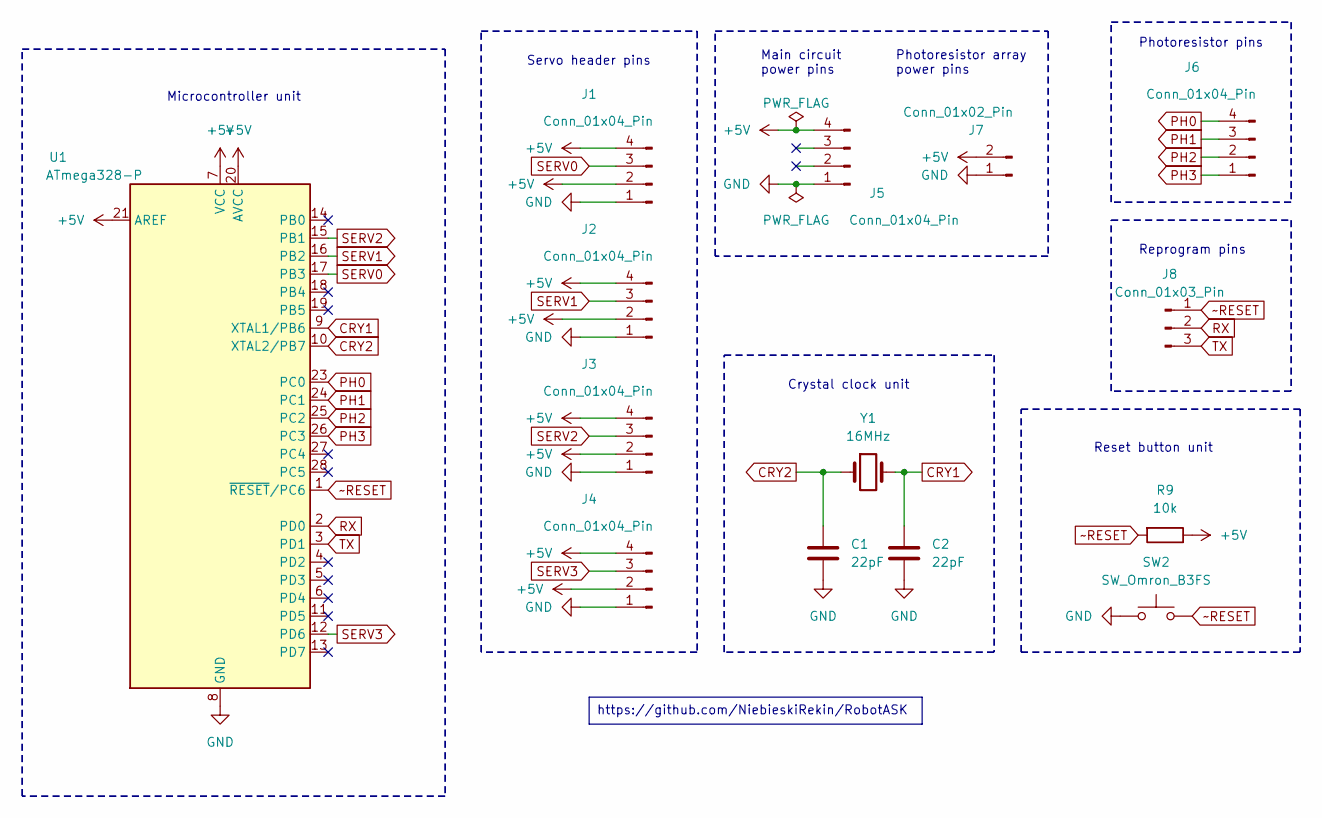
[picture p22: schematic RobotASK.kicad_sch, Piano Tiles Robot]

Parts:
C1, C2: 22pF; C_Disc_D3.8mm_W2.6mm_P2.50mm
J1, J2, J3, J4, J6: Conn_01x04_Pin; PinHeader_1x04_P2.54mm_Vertical
J5: Conn_01x04_Pin; USB-C Socket Breakout Board
J7: Conn_01x02_Pin; PinHeader_1x02_P2.54mm_Vertical
J8: Conn_01x03_Pin; PinHeader_1x03_P2.54mm_Vertical
R9: 10k; R_Axial_DIN0207_L6.3mm_D2.5mm_P10.16mm_Horizontal
SW2: SW_Omron_B3FS; SW_PUSH_6mm_H4.3mm
U1: ATmega328-P; DIP-28_W7.62mm
Y1: 16MHz; Crystal_HC49-4H_Vertical

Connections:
+5V: J1.2, J1.4, J2.2, J2.4, J3.2, J3.4, J4.2, J4.4, J5.4, J7.2, R9.1, U1.7 (VCC), U1.20 (AVCC), U1.21 (AREF)
CRY1: C2.1, U1.9 (XTAL1/PB6), Y1.2
CRY2: C1.1, U1.10 (XTAL2/PB7), Y1.1
GND: C1.2, C2.2, J1.1, J2.1, J3.1, J4.1, J5.1, J7.1, SW2.1, U1.8 (GND), U1.22 (GND)
PH0: J6.4, U1.23 (PC0)
PH1: J6.3, U1.24 (PC1)
PH2: J6.2, U1.25 (PC2)
PH3: J6.1, U1.26 (PC3)
RX: J8.2, U1.2 (PD0)
SERV0: J1.3, U1.17 (PB3)
SERV1: J2.3, U1.16 (PB2)
SERV2: J3.3, U1.15 (PB1)
SERV3: J4.3, U1.12 (PD6)
TX: J8.3, U1.3 (PD1)
~RESET: J8.1, R9.2, SW2.2, U1.1 (~RESET/PC6)

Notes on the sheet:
https://github.com/NiebieskiRekin/RobotASK
Photoresistor pins
Microcontroller unit
Reprogram pins
Crystal clock unit
Reset button unit
Main circuit power pins
Photoresistor array power pins
Servo header pins

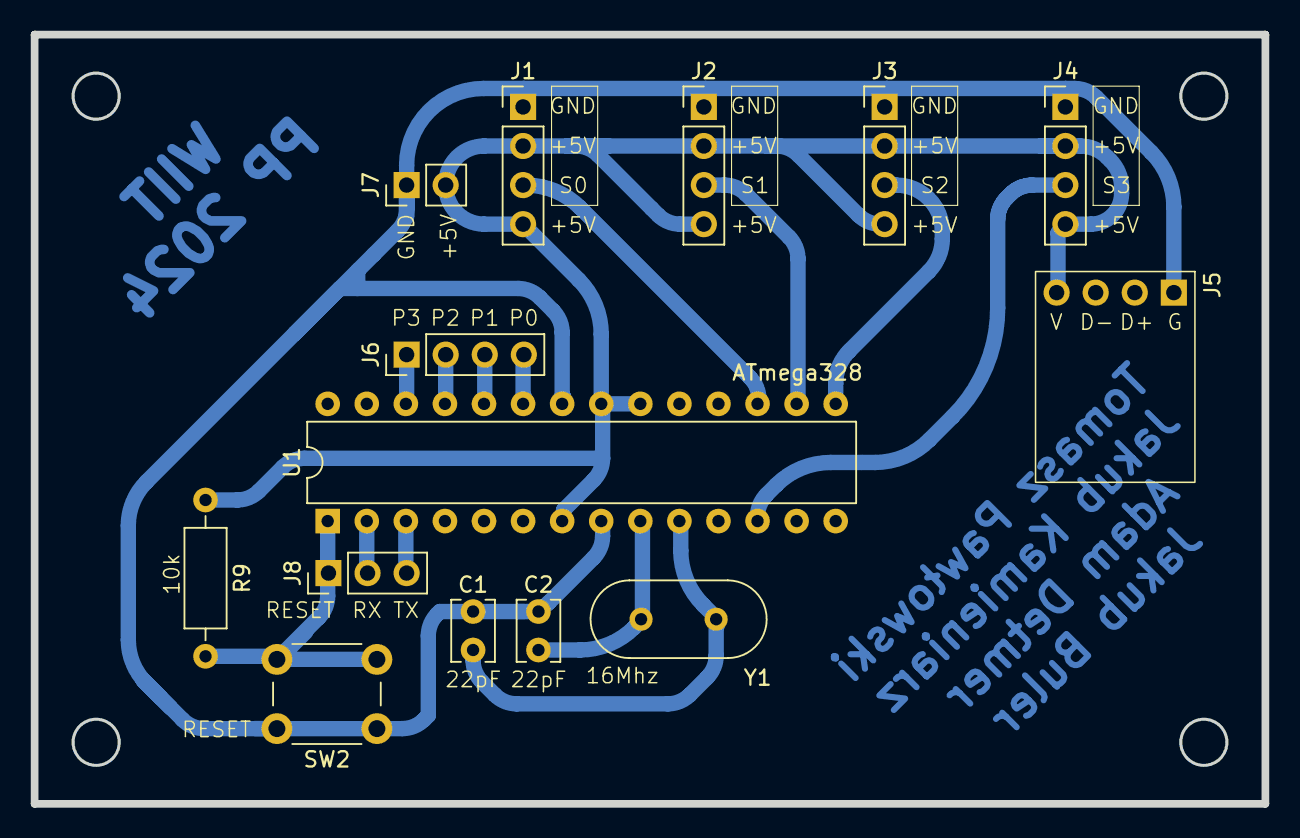
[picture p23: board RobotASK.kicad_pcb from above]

Board: 2 copper layers, 80.0 x 50.0 mm, 14 parts (0 on the bottom side), 15 nets.

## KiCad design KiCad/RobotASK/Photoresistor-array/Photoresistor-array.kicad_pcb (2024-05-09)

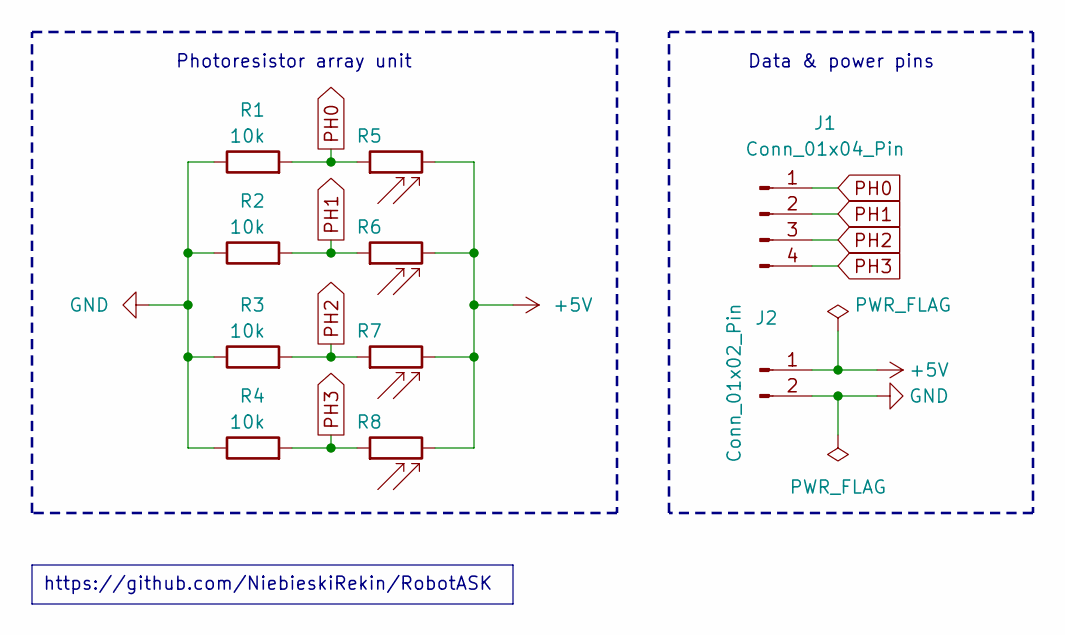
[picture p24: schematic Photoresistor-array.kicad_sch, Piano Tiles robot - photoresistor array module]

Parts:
J1: Conn_01x04_Pin; PinHeader_1x04_P2.54mm_Vertical
J2: Conn_01x02_Pin; PinHeader_1x02_P2.54mm_Vertical
R1, R2, R3, R4: 10k; R_Axial_DIN0207_L6.3mm_D2.5mm_P10.16mm_Horizontal
R5, R6, R7, R8: 5-10k; R_LDR_5.1x4.3mm_P3.4mm_Vertical

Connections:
+5V: J2.1, R5.2, R6.2, R7.2, R8.2
GND: J2.2, R1.1, R2.1, R3.1, R4.1
PH0: J1.1, R1.2, R5.1
PH1: J1.2, R2.2, R6.1
PH2: J1.3, R3.2, R7.1
PH3: J1.4, R4.2, R8.1

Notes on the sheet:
https://github.com/NiebieskiRekin/RobotASK
Data & power pins
Photoresistor array unit

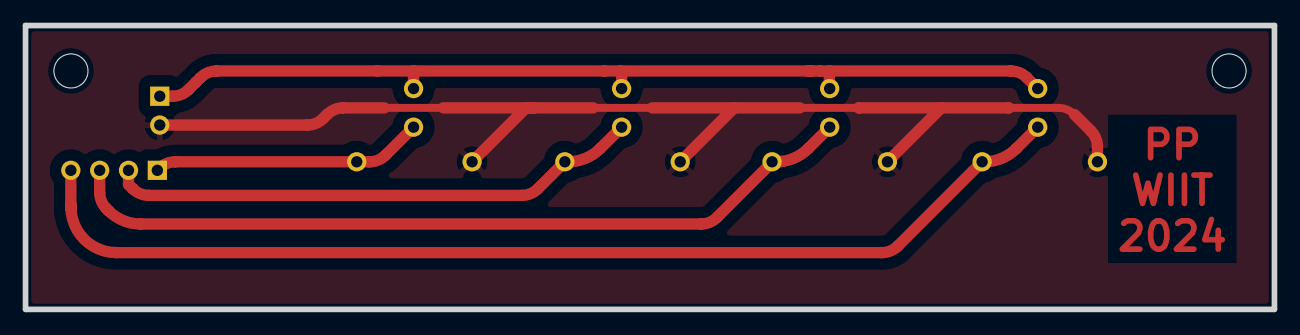
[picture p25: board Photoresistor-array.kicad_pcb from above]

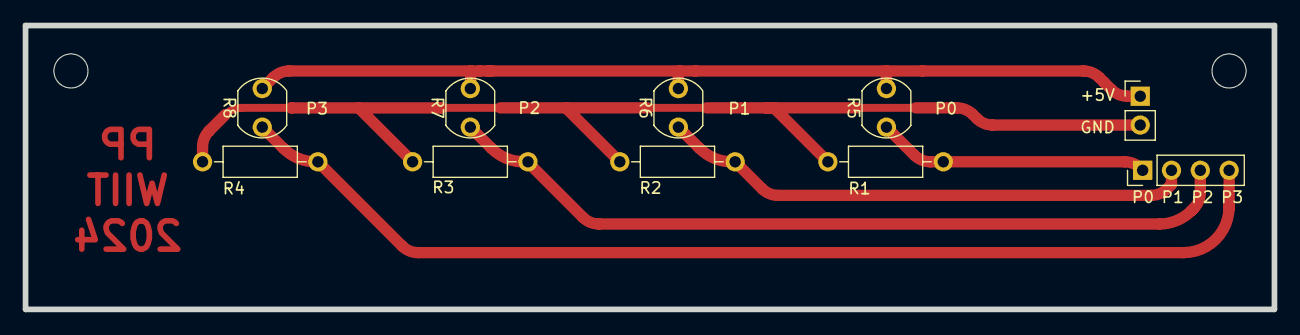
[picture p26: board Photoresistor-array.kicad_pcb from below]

Board: 2 copper layers, 110.0 x 25.0 mm, 10 parts (10 on the bottom side), 6 nets.

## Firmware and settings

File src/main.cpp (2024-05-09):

#define DEBUG 1
#include <Arduino.h>
#include <Servo.h>

// Defining the count of sensors and motor pairs and their corresponding pins
// (Change only if the layout of the board has changed)
constexpr size_t n = 4;                                     // count of sensor + servo pairs
constexpr uint16_t servo_pin[n] = {6, 9, 10, 11};           // servo motor pins (must be PWM~)
constexpr uint16_t photoresistor_pin[n] = {A0, A1, A2, A3}; // photoresitor pins (must be analog)

// Program specific variables and objects
Servo servos[n];                            // Servo object used by the Servo library
uint32_t last_photoresistor_check[n] = {0}; // Last time the photoresistor value was read, modified in loop
int last_servo_degrees[n] = {0};            // Last angle the servomotor was set to, modified in loop
int servo_released_degrees[n] = {0};        // Angle at which the servo's handle doesn't touch the screen, modified in setup
uint32_t temp_time = 0;                     // Temporary variable that stores time passed between servo presses, modified in loop
uint16_t photoresistor_value = 0;           // Temporary variable that stores values read by the photoresistor, modified in loop
#ifdef DEBUG
const int bufsize = 128; // Size of the buffer for storing data coming from Serial
char buffer[bufsize];    // Input buffer for receiving data from Serial
#endif

// ╔───────────────────────╗
// │Adjust parameters below│
// ╚───────────────────────╝

// If the measurement value read by photoresistor 'i' is lower than the *threshold* then the servo 'i' moves.
uint16_t thresholds[n] = {600, 600, 600, 600}; // Default {500,500,500,500}, Possible integer values 0-1023

// Starting value of delay between reading from the same photoresistor in miliseconds (1/1000 s).
uint32_t start_delay_ms = 10; // Default 100, Possible integer values >0

// The angular displacement ( released angle - pressed angle) for each servomotor's handle when a black tile is detected. Servos spin counterclockwise.
int servo_pressed_degrees_delta[n] = {5, -16, 16, -8}; // Default {5, -5, 5, -5}, Possible values such that always (released+delta) in [0°; 180°]
// ─────────────────────────

#ifdef DEBUG

int wait_upto_10s_for_input()
{
  uint32_t time_start = millis();
  while (Serial.available() == 0)
  {
    // wait up to 10s for input on serial
    if (time_start + 10000 < millis())
    {
      return 0;
    }
  }
  return 1;
}

void receive_values_of_parameters_from_serial()
{
  if (wait_upto_10s_for_input())
  {
    memset(buffer, 0, bufsize * sizeof(char)); // clear buffer contents
    Serial.readBytesUntil('\n', buffer, bufsize);
    switch (buffer[0])
    {
    case '.': // 'p' for photoresistor thresholds
      // . 200,600,200,600 ; 10 ; 19,-25,17,-15
      sscanf(buffer, ". %u,%u,%u,%u ; %lu ; %d,%d,%d,%d",
             &thresholds[0], &thresholds[1], &thresholds[2], &thresholds[3],
             &start_delay_ms,
             &servo_pressed_degrees_delta[0], &servo_pressed_degrees_delta[1],
             &servo_pressed_degrees_delta[2], &servo_pressed_degrees_delta[3]);
      break;
    default:
      return; // abandon filling other values
    }
  }
}

#endif

// Only run once
void setup()
{
#ifdef DEBUG
  // Opening serial port for calibration and debugging
  Serial.begin(115200);

  receive_values_of_parameters_from_serial();

  for (size_t i = 0; i < n; i++)
  {
    Serial.print(String(thresholds[i]) + " ");
  }

  Serial.print("\n" + String(start_delay_ms) + "\n");

  for (size_t i = 0; i < n; i++)
  {
    Serial.print(String(servo_pressed_degrees_delta[i]) + " ");
  }

  Serial.print("\n");

#endif

  // Fill program specific arrays with all 0
  memset(last_photoresistor_check, 0, n * sizeof(uint32_t));
  memset(last_servo_degrees, 0, n * sizeof(int));
  memset(servo_released_degrees, 0, n * sizeof(int));

  for (size_t i = 0; i < n; i++)
  {
    // Assingning Analog pins to read data from photoresistor
    pinMode(photoresistor_pin[i], INPUT);
    // Attaching servo pins to allow for control
    servos[i].attach(servo_pin[i]);
    // Setting the default position
    servo_released_degrees[i] = servos[i].read();
    // Release all servos
    servos[i].write(servo_released_degrees[i]);
  }

#ifdef DEBUG
  for (size_t i = 0; i < n; i++)
  {
    Serial.print(String(servo_released_degrees[i]) + " ");
  }
  Serial.print("\n");
#endif

  delay(1000);

  // Press down all servo handles at once
  for (size_t i = 0; i < n; i++)
  {
    servos[i].write(servo_released_degrees[i] + servo_pressed_degrees_delta[i]);
  }

#ifdef DEBUG
  // Print starting time
  Serial.println(millis());
#endif

  // Hold shortly
  delay(100);

  // Release all servo handles and begin loop
  for (size_t i = 0; i < n; i++)
  {
    servos[i].write(servo_released_degrees[i]);
  }
  delay(100);
}

// Run indefinitely in a loop
void loop()
{

  // For each pair `i` we check sequentially that ...
  for (size_t i = 0; i < n; i++)
  {

    // if the time since last value read for that specific photoresistor `i` was read
    // is less than start_delay_ms
    if (((temp_time = millis()) - last_photoresistor_check[i]) > start_delay_ms)
    {
      last_photoresistor_check[i] = temp_time; // reset timer

#ifdef DEBUG
      Serial.print(String(temp_time) + " ");
#endif

      // check if the photoresistor `i` value is less than the threshold parameter
      // Note that the threshold value should be adjusted
      // In other words, this if clause detects black tiles
      if ((photoresistor_value = analogRead(photoresistor_pin[i])) < thresholds[i])
      {
        // Move the servomotor handle to press on the screen
        last_servo_degrees[i] = servo_released_degrees[i] + servo_pressed_degrees_delta[i];
      }
      else
      {
        // Move back the servomotor handle to release the tap
        last_servo_degrees[i] = servo_released_degrees[i];
      }

#ifdef DEBUG
      // Print the value read by photoresistor to the serial monitor
      Serial.print(String(i) + " " + String(photoresistor_value) + "\n");
#endif
    }

    // save last handle position until the next check
    servos[i].write(last_servo_degrees[i]);
  }
}

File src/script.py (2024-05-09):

#!/bin/python3

# export QT_QPA_PLATFORM=xcb 

# TODO: time scale
# TODO: wartosci
# TODO: zmniejszenie jitter / implementacja smooth scrolling za pomocą shift (klatki przejściowe pomiędzy skokami dużych pikseli / bloczków)

# Required dependencies
# pip install pyserial opencv-python numpy
import serial
import numpy as np
import time
import cv2

thresholds = [600, 600, 600, 600]
delay = 25
servos = [5, -16, 16, -8]
timestart = 0


port = "/dev/ttyACM0"
baudRate = 115200
serialCom = serial.Serial(port, baudRate, timeout=10, write_timeout=10) # open a serial connection
n = 360_000 # rows of the history
rows = 40 #  rows of the preview
title = "Wizualizacja danych z robota" # title of the window
bilateral_filtering = False



# data = np.random.randint(1024,size=(n*rows,4),dtype=np.uint16)
iters = [0, 0, 0, 0] # pointers to the next row to fill for each column, could be simplified
data = np.full((n*rows,4),1024,dtype=np.uint16) # full history of measurements

def get_slice(i): 
    # Get a slice of data expressed as rbg triplets ready for rendering

    i = max(rows,i)
    part = data[i-rows:i, :] # get a slice of data ending at location i
    newpart = np.where(part == 1024, 122, np.where(part < thresholds, 0, 255)) # convert measurement values to single channel rgb
    return np.repeat(newpart[:,:, np.newaxis], 3, axis=2).astype(np.uint8) # convert single channel rgb to tripple and change type to match opencv
 

def animate(line):
    # Convert an incoming line from serial to a frame 

    # line[0] - time
    # line[1] - column
    # line[2] - measurement value

    if line is None: # line from serial has corrupted data, just re-render the same frame 
        return get_slice(max(iters))
    a = line[1] # which photoresistor (column)
    i = iters[a]
    data[i, a] = line[2] # fill the correct column at next available row with value from the measurement
    iters[a] += 1 # increase column pointer
    return get_slice(i) # render a frame with updated data with i+1 row downmost
   
def read_line_serial():
    # read a line from serial, none if corrupted (lazy check)
    line = get_photoresistor_measurement(read_bytes_string())
    if line[1] < 0 or line[1] > 3: # column bounds check and exclude c
        return None
    elif line[2] < 0 or line[2] > 1023: # check if measurements make sense
        return None
    # note no time check
    print(string_photores(line))
    return line


def get_photoresistor_measurement(input):
    # Parse string to get 3 ints or return [-1, -1, 1024]
    if input != "":
        try:
            values = [int(x) for x in input.split()]
            if len(values) == 3:
                return values
        except ValueError:
            pass
    return [-1, -1, 1024]

def get_thresholds(input="", thresholds=thresholds):
    # Parse string to get 4 ints or return default value
    if input != "":
        try:
            values = [int(x) for x in input.split()]
            if len(values) == 4:
                return values
        except ValueError:
            pass
    return thresholds

def get_time(input="", time1=delay):
    # Parse string to get an int or return default value
    if input != "":
        try:
            return int(input)
        except ValueError:
            pass
    return time1

def get_servos(input="", servos=servos):
    # Parse string to get 4 ints or return default value
    if input != "":
        try:
            values = [int(x) for x in input.split()]
            if len(values) == 4:
                return values
        except ValueError:
            pass
    return servos


def read_bytes_string():
    # Read incoming bytes from serial as string
    try:
        s_bytes = serialCom.readline()
        return s_bytes.decode("ascii").strip()
    except serial.SerialException:
        return ""


def live_view(bilateral_filtering):
    while True:
            line = read_line_serial()
            # line = [0,random.randint(0,3),random.randint(0,1023)]
            image = cv2.resize(animate(line), dsize=(1000, 1200), interpolation=cv2.INTER_NEAREST)
            if bilateral_filtering:
                # a convolution would be much better honestly
                image = cv2.GaussianBlur(image, (15,15),0)
                # image = cv2.bilateralFilter(image,5,75,75) # apply a blur in one direction basically
            cv2.imshow(title, cv2.flip(image,0))
            k = cv2.waitKey(1)
            if k == 27: # esc
                scrollable_view()
            elif k == ord('b'):
                print("bilateral_filtering: On")
                bilateral_filtering = True 
            elif k == ord('n'):
                print("bilateral_filtering: Off")
                bilateral_filtering = False 



def scrollable_view():
    serialCom.close()
    current_row = max(iters)
    max_row = current_row+1
    print("Esc to exit")
    print("w - scroll up, s - scroll down")
    while True:
        image = cv2.resize(get_slice(current_row), dsize=(1000, 1200), interpolation=cv2.INTER_NEAREST)
        cv2.imshow(title, cv2.flip(image,0))
        k = cv2.waitKey(1)
        if k == 27: # esc
            try:
                pass
            finally:
                cv2.destroyAllWindows()
                serialCom.close()
            exit()
        elif k==ord('w'): # up
            current_row = max(current_row-1,rows)
        elif k==ord('s'): # down
            current_row = min(current_row+1, max_row)


def string_list(input_list):
    s = ""
    for i in input_list:
        s += f"{i:>6}|"
    return s

def string_photores(input_list):
    s = f"|{(input_list[0]):>6}|"
    for i in range(input_list[1]):
        s+= "      |"
    if (input_list[2] < thresholds[input_list[1]]):
        s += f"{input_list[2]:>5}*|"
    else:
        s += f"{input_list[2]:>6}|"
    for i in range(3-input_list[1]):
        s+= "      |"
    return s
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

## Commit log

2024-05-09 Schematic and PCB
    [Photoresistor-array.kicad_pcb, Photoresistor-array.kicad_sch, RobotASK.kicad_pcb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]
2024-05-09 PCB renders (images and 3D models)
    [Photoresistor-array.step]
2024-05-09 Add pins to quickly reprogram the microprocessor
    [RobotASK.kicad_pcb, RobotASK.kicad_sch]
2024-05-09 Main pcb .step export
2024-05-09 Remove redundant GND pin & migrate to KiCad8
    [RobotASK.kicad_pcb, RobotASK.kicad_sch, usb-c-socket.step]
2024-05-09 Add .step 3D exports with traces
    [Photoresistor-array.step]
2024-05-09 Add manual PCB etching checklist
2024-05-09 Edit pcb layers
    [Photoresistor-array.kicad_pcb, RobotASK.kicad_pcb]
2024-05-09 Update 3D .step exports
    [Photoresistor-array.step]
2024-05-09 Add gerber files and prints for manual etching
    [Photoresistor-array-B_Cu.gbr, Photoresistor-array-Edge_Cuts.gbr, Photoresistor-array-F_Cu.gbr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]
2024-05-09 Add a bill of materials needed for PCB etching
2024-05-09 Update manual PCB etching checklist
    Update ListaPCB.md
2024-05-09 Make photoresistor PCB single layer
    The printed circuit board of the photoresitor array submodule was
    increased in length to accomodate the power and signal goldpins on the
    same side as the resistors and photoresistors. This allows us to make
    a single layer PCB, which is much easier handmade.
    [Photoresistor-array.kicad_pcb, Photoresistor-array.step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]
2024-05-09 Add procedure for PCB etching using photosensitive film
2024-05-09 Update servo pins & code formatting
2024-05-09 Add code that uses coins instead of servos
    Alternative version of the project that uses coins to which voltage is
    applied as a means to register touch press on a screen in order to
    replace somewhat complicated servo physical limitations.
2024-05-09 Widen all possible traces, fill edge cuts layer, widen photoresistor PCB by 2mm
    [Photoresistor-array.kicad_pcb, RobotASK.kicad_pcb]
2024-05-09 Increase the size of component holes and pads
    [Photoresistor-array.kicad_pcb, Photoresistor-array.kicad_sch, RobotASK.kicad_pcb]
2024-05-09 Add new PCB prints (toner etching & drilling), order old ones
    Added new prints exports of the PCB for the heat toner transfer method and drilling holes. Ordered old prints for the method using photosensitive film
2024-05-09 Refresh PCB backups
2024-05-09 Add communication over serial port
    Added the option of changing program parameters at during the first 10s of runtime. Added a pretty print of the values read by the robot over serial. Baud rate set to 115200 bauds.
2024-05-09 Prettify the PCB and create renders
    [Photoresistor-array.kicad_pcb, Photoresistor-array.kicad_sch, Photoresistor-array.step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]
2024-05-09 Add a script that visualises photoresistor reads
    Added a python script that displays an image that resembles the game
    screen based on the photoresitor measurements for each frame.
    Required dependencies: `pip install pyserial opencv-python numpy`
    The main code running on the ATmega328 was simplified, all of the
    terminal pretty printing was moved to the script. Debug serial output
    from the microprocessor is minimal.
